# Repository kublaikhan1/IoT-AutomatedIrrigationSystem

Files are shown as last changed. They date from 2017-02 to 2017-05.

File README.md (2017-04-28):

## Concept Proposal

### High-level Concept:
Create an IoT indoor home irrigation system for potted plants using a Raspberry Pi and various hardware components. The system will feature two soil moisture sensors in two separate potted plants that will send real time analog data back to the Pi. Software on the Pi will monitor these sensor levels periodically; when levels fall below a certain threshold that constitutes “dry” soil, a signal will be sent to activate a peristaltic pump attached to the Pi. The pump will distribute water from a plastic reservoir to the plants that are “dry” (i.e. either one or both) until the moisture sensor input rises above the threshold, at which point the pump will deactivate. Sensor readings and water usage data will be viewable via a ThingSpeak interface as well as notifications from Twitter. Having two sensor/plant setups will hold as a proof of concept that multiple plants and sensors can be linked into this IoT system. 

## Operation and Interaction:
This project will stand out among other competitive irrigation systems by our ability to connect multiple separate potted plants. Other projects made watering systems for either one plant, or a single bed of many plants, so the challenge here is to maintain two or more individual plants. 

Using different plants requires the use of solenoid valves that can redirect the flow of water to the proper plant. The pump and the valves require 12VDC, which is more than the output of the RPi’s 5VDC, so a relay will be used to connect these devices with the Pi. When a valve needs to be opened and the pump turned on, the Pi will send 5VDC to the relay, which will enable the hardware on the other side of the relay. 

The soil moisture sensors record data in analog, which is not standard for the Pi, so an MCP3008 chip will be used, which takes up to eight separate analog inputs at a time, converting them to digital. Although we will only be proving the irrigation system works for two plants (i.e. two analog sensors), up to eight will be feasible using this chip.
One additional sensor will be placed in the water reservoir where the pump is located - a water level float switch. When the water level drops to a certain point, the sensor will trip, sending a signal to the Pi. We will link this with Twitter as well to send a notification to the user that the reservoir needs to be refilled.

## Required Hardware:
1. RPi - in this case, we’ll be using Elliot’s RPi2 and Hamad’s RPi3
2. 2x Analog Capacitive soil moisture sensors
3. 2x Solenoid valves 12VDC
4. 1x Peristaltic pump 12VDC
5. 1x MCP3008 chip for analog to digital conversion
6. 1x 5VDC 4-channel relay
7. 1x Water level sensor

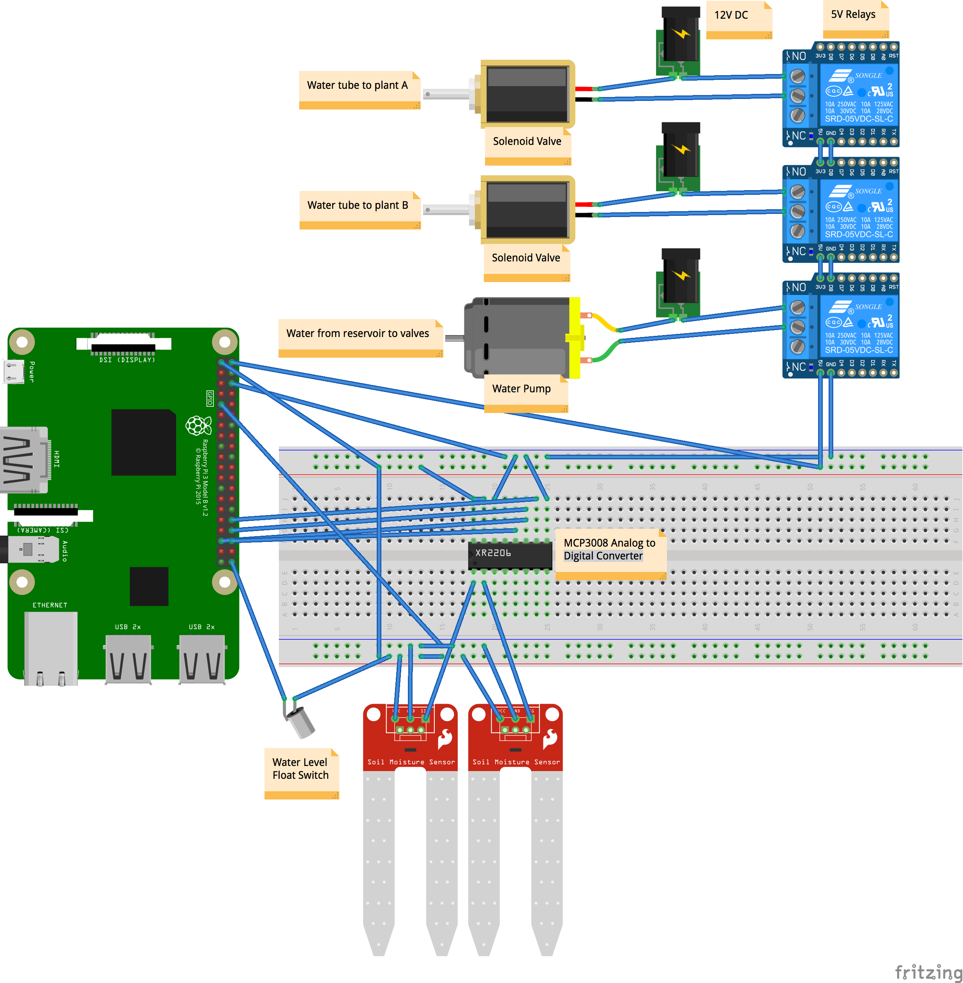
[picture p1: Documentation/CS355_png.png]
Optional Title


# Contributors
@hamadkh
@giese

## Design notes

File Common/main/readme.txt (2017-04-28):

/*
Module: Communication with ThingSpeak (on Linux) via TCP Socket
Author:  Pedro Bertoleti
Modified by: Hamad Khawaja, Elliot Giese
*/

INFORMATION FOR THINGSPEAK CHANNEL 
------------------------------------------

run:
----
make

./ThingSpeakC APIKEY [field1] [field2] ....... [fieldn]

CURRENT TEST APIKEY: 1J6Q9XGCJ3FJ456A

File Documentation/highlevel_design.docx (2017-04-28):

Elliot Giese

Hamad Khawja

CS 355 - Systems Programming

Part 2 - System Design

On it’s own, the Raspberry Pi can not read incoming analog data on GPIO pins. Since this irrigation system utilizes analog soil moisture sensors, an analog-to-digital converter is required. An MCP3008 chip is used to convert up to eight analog inputs into digital inputs for the Pi to read, and can either run on the Pi’s SPI hardware bus, or implemented on SPI via software. The diagram below depicts only two analog sensors connected to the chip, for the sake of space; however, up to eight can be used with this MCP3008 chip. Both the chip and the soil moisture sensors take 3.3V of power from the RPi 3V3 pin.

The soil sensors will periodically (~every 15 minutes) gather data values between 0 - 600 (with 0 constituting dry soil, and 600 wet) from each connected plant to send to the Pi. Based on programming logic enforced in a C-based program, the Pi will make a decision during these intervals to water the plant(s) or not. If the moisture value of a plant falls below a defined constant threshold (based on the type of plant input to the program on runtime), the Pi will turn on a water pump and particular solenoid valve associated with the dry plant.

Solenoid valves require 12VDC to activate, and are closed when power is off, and open when supplied power. The pump utilizes 120VAC, and is automatically on when plugged in (there is no on-off switch). By default, it’s flow rate is 80 gal/hr, but this can be adjusted manually with a dial on the side. Both solenoid valves and the pump will be connected to a 4-channel 5VDC relay, which in turn is connected to the Pi.

A 4-channel relay operates on 5VDC, which will be taken from the 5VDC pin on the Pi. Three GPIO pins, and GND will connect from the Pi to the relay. When the Pi sends a signal to turn on the pump over the GPIO line, 5VDC will activate the pump and valve relays. Relays allow low-power (5VDC) circuits to switch on higher-power (12VDC - 220VAC) circuits - in this case, the relay will activate the pump and one or both of the pump circuits. The pump will distribute water to one or both plants in short intervals until the next sensor reading returns a moisture value that has returned above the threshold. Flyback diodes may need to be included on the Pi side of the relay, as well as the pump and valve sides to prevent current from re-entering the devices in the wrong direction, damaging it.

Finally, a water float switch will be connected to the 3V3 pin of the Pi as well as a GPIO pin, which will monitor the water level of the basin that the pump is drawing water from. When the basin level falls below a certain value, the float switch will trip, sending a signal to the Pi. Upon receiving the signal, the Pi will send a Tweet to the user, informing them that the water levels are low, and should be refilled.

Collecting data from and interacting with GPIO pins in C will require including an open source library called wiringPi. Data interaction will be done via ThingSpeak, where the user can view daily summaries of water usage, power consumption, moisture levels, and watering times.

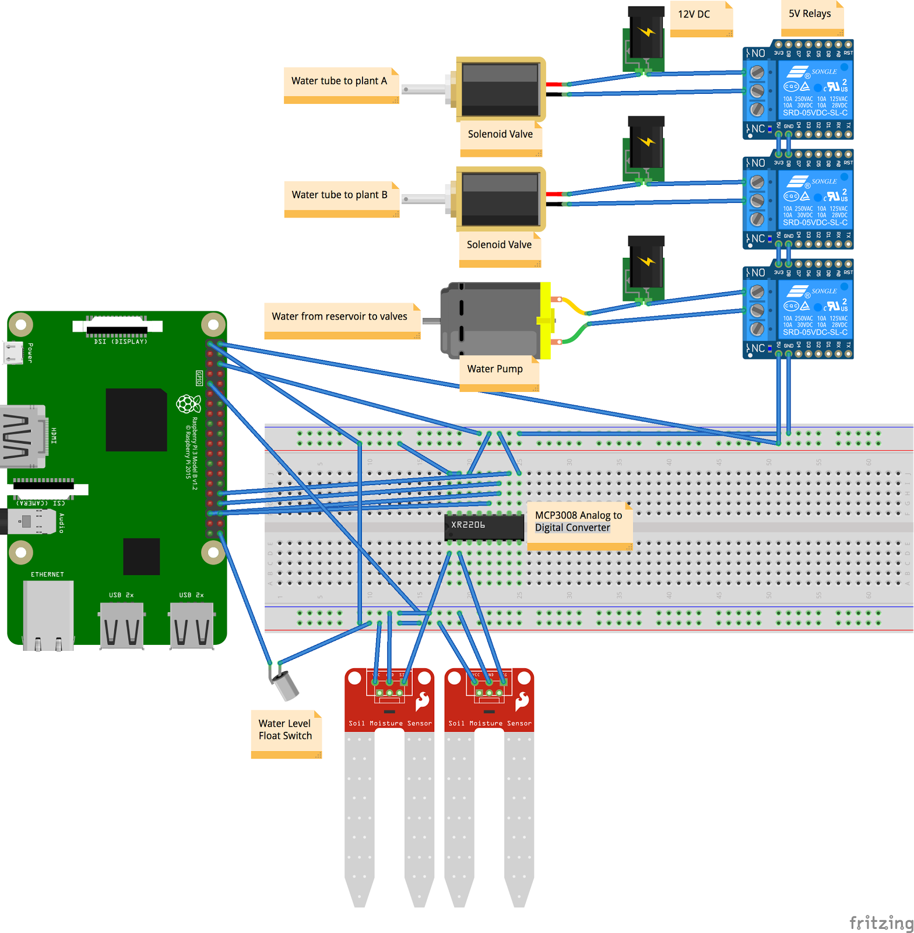
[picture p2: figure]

Wiring diagram of the circuit. Soil moisture sensors will be inserted into individual potted plants. Float switch will be in the reservoir of water. ½” clear vinyl tubing connects the pump to a T-joint, which in turn connects both of the solenoid valves. Valves use ½” male x ½” barbed connectors to attach vinyl tube, which then goes to plant. Each plant has one valve and one sensor associated.

BASIC FLOWCHART:

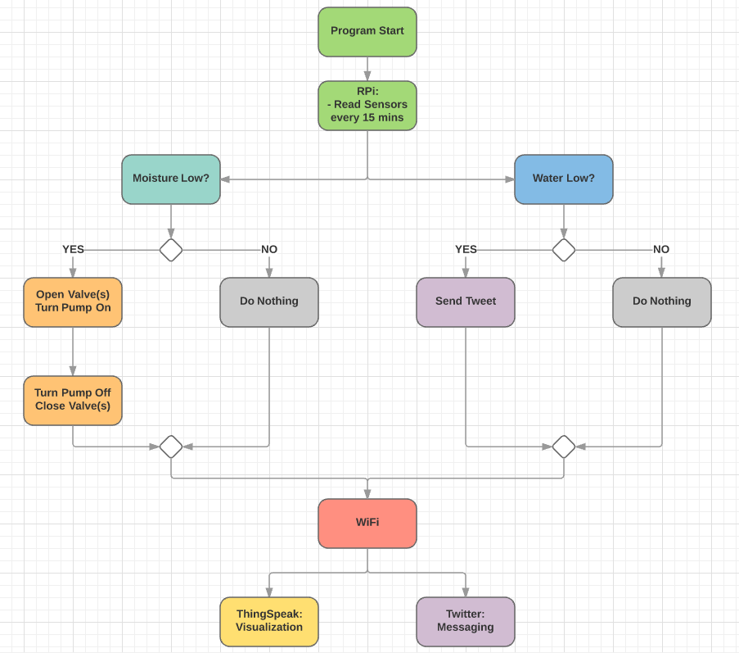
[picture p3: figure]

DATA FLOW:

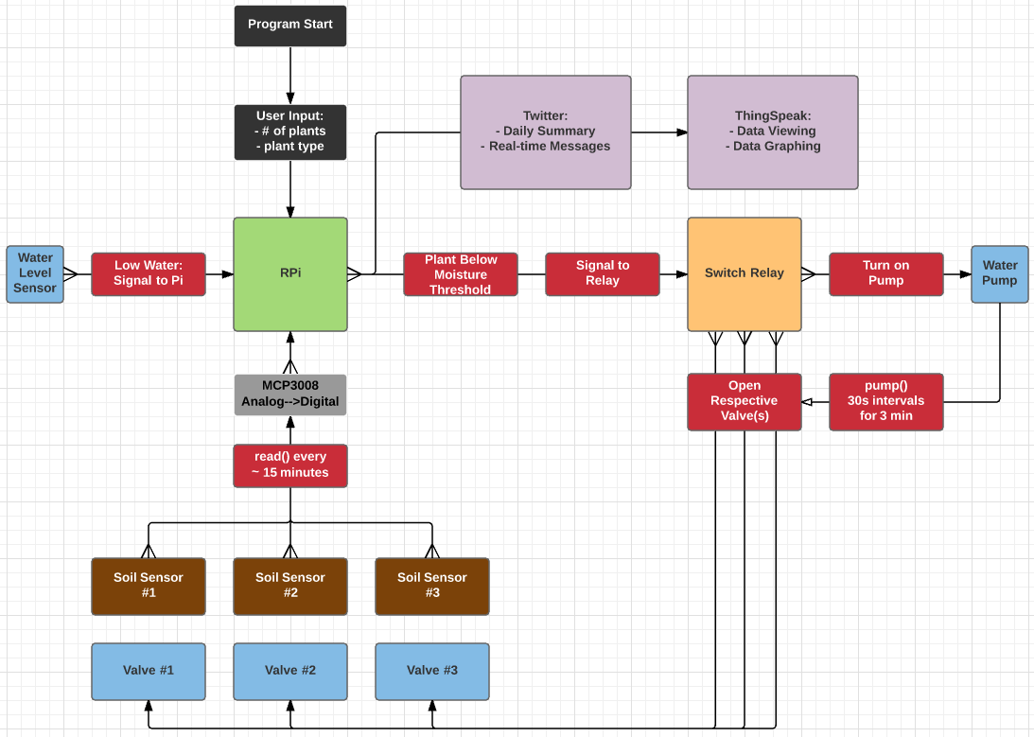
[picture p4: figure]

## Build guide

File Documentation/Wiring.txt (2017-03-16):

LCD Display
1  VSS  - Ground
2  VDD  - 5VDC
3  V0   - Ground
4  RS   - GPIO26, or PIN 24 on wiringPi, PIN 37 header
5  RW   - Ground
6  E    - GPIO21, or PIN XX on wiringPi, PIN 40 header
7  D0   - SKIP
8  D1   - SKIP
9  D2   - SKIP
10 D3   - SKIP
11 D4   - GPIO20, or PIN XX on wiringPi, PIN 38 header
12 D5   - GPIO16, or PIN XX on wiringPi, PIN 36 header
13 D6   - GPIO12, or PIN XX on wiringPi, PIN 32 header
14 D7   - GPIO25, or PIN XX on wiringPi, PIN 22 header
15 A    - 5VDC
16 K    - Ground

Float switch
When magnet is at bottom (low on water), circuit closes - i.e.
HIGH VOLTAGE
When magnet is floating at top (water level is good), circuit open - i.e.
LOW VOLTAGE
Pin 8 (4 on wiring)
Ground

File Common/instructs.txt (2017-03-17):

BY: HAMAD KHAWAJA

Installing GTK+ Library on RaspberryPi Linux
--------------------------------------------

sudo apt-get install libgtk2.0-dev
sudo apt-get install libgtk-3-dev

echo `pkg-config --cflags --libs gtk+-3.0`

Installing Glade
----------------

sudo apt-get install glade (GUI EDITOR)

Installing Geany
----------------

sudo apt-get isntall geany (TEXT EDITOR/ NOT MANDATORY)

Dependencies
------------
gcc -o main gui.c `pkg-config --cflags --libs gtk+-3.0`

running using make 
------------------

make 
make clean

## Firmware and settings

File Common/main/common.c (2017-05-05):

#include <time.h>
#include <stdio.h>
#include <stdlib.h>
#include <stdint.h>
#include <unistd.h>
#include <mcp3004.h>
#include <pthread.h>
#include <wiringPi.h>
#include "ThingSpeakLinux.h"


/* Definitions for MCP3004/8 chipset */
#define BASE 100
#define SPI_CH 0

/* Definitions for 4-chan relay GPIO pins */
#define RELAY1 21
#define RELAY2 22
#define RELAY3 23
#define RELAY4 24

/* Float Switch GPIO pin */
#define FL_SWI 4

/* Define number of plants */
#define NUM_PLANTS 2

/* Definitions for DHT22 temp/hum sensor */
#define MAX_TIMINGS 85
#define DHT_PIN 5

void start();
int getWaterLevel();
void *soilThread();
void getSoilMoisture(int[],float[]);
double getWaterUsage(double);
void read_dht_data();
void temperatureReadings();
void activateRelays();

int data[5] = { 0, 0, 0, 0, 0 };
int soilVals[NUM_PLANTS] = {1000};
float soilPercent[NUM_PLANTS] = {100.0};
float humtemp[3] = {0.0};
float FieldsArrayPlant1[6]={0.0};
float FieldsArrayPlant2[6]={0.0};
int waterLvl;



int main(void)
{
	pthread_t pt;

	if(wiringPiSetup() == -1)
	{
		printf("wiringPi setup failed");
		return 1;
	}
	
	start();
	pthread_create(&pt, NULL, soilThread, NULL);
	
	int count = 1;
	
	while(count == 1)
	{		
		if(!waterLvl)
		{
			
			//printf("Exiting program!\n");
			//count++;
			//exit(1);
		}
		
		//activateRelays();
		sleep(5);
	}

	return 0;
}


/* ------------------------------------------------
 * Initialize Analog-to-Digital Converter
 * Initialize GPIO pin modes for each relay
 * Initialize GPIO pin for float switch
 * -----------------------------------------------*/
 
void start()
{
	digitalWrite(FL_SWI, HIGH);
	mcp3004Setup(BASE, SPI_CH);
	pinMode(RELAY1, OUTPUT);
	pinMode(RELAY2, OUTPUT);
	pinMode(RELAY3, OUTPUT);
	pinMode(RELAY4, OUTPUT);
	pinMode(FL_SWI, OUTPUT);
}


/* ------------------------------------------------
 * Returns 0 if water level is low, 1 otherwise
 * -----------------------------------------------*/
 
int getWaterLevel()
{
	return digitalRead(FL_SWI);
}


/* ---------------------------------------------------------------
 * Reads channels 0-7 on MCP3008 chip over Serial 
 * Peripheral Interface (SPI).
 * Each analogue sensor returns a value from 0 ~ 600
 * Value of    0 is dry (i.e. air)
 * Value of ~600 is wet (i.e. pure water)
 * --------------------------------------------------------------*/
 
void getSoilMoisture(int soilVals[], float soilPercent[])
{
	int chan, i;
	int sum = 0;
	
	for(chan = 0; chan < NUM_PLANTS; ++chan)
	{
		
		for(i = 0; i < 2000; i++)
			sum += (1023 - analogRead(BASE + chan));
			
		soilVals[chan] = sum / 2000;
		soilPercent[chan] = (float) ((soilVals[chan] / 800.0) * 100.0);

		if(soilVals[chan] < 800)
			printf("PLANT #%d moisture: %3.2lf%\n", chan+1, soilPercent[chan]);
		
		sum = 0;	
	}
}


/* ------------------------------------------------
 * Returns the amount of water  
 * used by the pump in Liters
 * Pump waters at a rate of 300L/H
 * timeWatered is recorded in seconds
 * -----------------------------------------------*/
 
double getWaterUsage(double timeWatered)
{
	return 300 * timeWatered / 3600;
}


/* ------------------------------------------------
 * Thread function which will collect the soil data  
 * and temperature data
 * If the water level is LOW, then the thread will
 * die
 * -----------------------------------------------*/
 
void *soilThread()
{
	char apiKey1[] = "KQ0EYMR9E7QY7500";
	char apiKey2[] = "Z8725FTQG09C3FIK";
	
	while(1)
	{
		printf("Water Level = %d\n\n", waterLvl = getWaterLevel());
		if(!waterLvl)
		{
			printf("---  Water level is low  ---\n");
			printf("--- Pump will not activate ---\n\n");
		}
		getSoilMoisture(soilVals, soilPercent);
		temperatureReadings();
		
		activateRelays();
		
		int i;
		for(i = 0; i < 6; i++)
		{
			SendDataToThingSpeak(6, &FieldsArrayPlant1[i],apiKey1,sizeof(apiKey1));
			SendDataToThingSpeak(6, &FieldsArrayPlant2[i],apiKey2,sizeof(apiKey2));
		}
		
		printf("\n-------------------------------------------\n\n");
		
		sleep(3);
	}

	return NULL;
}


/* -----------------------------------------------------
 * Function to take 250 temperature / humidity  
 * readings based on the read_dht_data() function
 * The sensor's data is sometimes corrupt, which is the
 * result of a faulty sensor - even the read_dht_data()
 * function accounts for this... So 250 measurements
 * will ensure that at least one value is recorded
 * ----------------------------------------------------*/
 
void temperatureReadings()
{
	int count = 0;
	while(1)
	{
		read_dht_data();
		if( !( humtemp[0] == 0.0 || humtemp[1] == 0.0 || humtemp[2] == 0.0 ) || (humtemp[0] >= 100.0 || humtemp[1] >= 100.0) || count > 249)
		{
			break;
		}
		count++;
	}
}


/* ----------------------------------------------------
 * Function to turn on the relays, which are connected
 * to the solenoid vales and the water pump.
 * If the soil moisture percentage is lower than 50%
 * for a given plant, the relay/valve associated with
 * that plant will open, and the pump will turn on.
 *
 * Function also records amount of water used, and
 * length of time that plants were watered.
 * ---------------------------------------------------*/
 
void activateRelays()
{
	double timeWatered = 0.0; double amtWatered = 0.0;
	int relays[] = {RELAY1,RELAY2,RELAY3,RELAY4};
	int numPlantsWatered=0; int numRelays=4;
	time_t waterTimeStart, waterTimeEnd;
	int i;
	
	for(i = 0; i < NUM_PLANTS; i++)
	{
		if(soilPercent[i] < 50.0 && waterLvl)
		{
			time(&waterTimeStart);
			digitalWrite(relays[i], LOW);
			digitalWrite(relays[2], LOW);
			printf("PLANT valve #%d open\n", (i+1) );
			//printf("PUMP ON \n" );
			
			delay(5000);
			
			digitalWrite(relays[i], HIGH);
			digitalWrite(relays[2], HIGH);
			printf("PLANT valve #%d closed\n\n", (i+1) );
			//printf("PUMP OFF \n");
			
			time(&waterTimeEnd);
			timeWatered = difftime(waterTimeEnd, waterTimeStart);
			amtWatered += getWaterUsage(timeWatered);
			numPlantsWatered++;
		}
	}
	
	// Fill ThingSpeak Arrays
	FieldsArrayPlant1[0] = soilPercent[0];
	FieldsArrayPlant1[1] = humtemp[2];
	FieldsArrayPlant1[2] = humtemp[0];
	FieldsArrayPlant1[3] = timeWatered;
	FieldsArrayPlant1[4] = amtWatered;
	FieldsArrayPlant1[5] = waterLvl;
	
	FieldsArrayPlant2[0] = soilPercent[1];
	FieldsArrayPlant2[1] = humtemp[2];
	FieldsArrayPlant2[2] = humtemp[0];
	FieldsArrayPlant2[3] = timeWatered;
	FieldsArrayPlant2[4] = amtWatered;
	FieldsArrayPlant2[5] = waterLvl;
	
	if(waterLvl)
	{
		printf("Time watered: %.2lf seconds\n", timeWatered*numPlantsWatered);
		printf("Amount of water used: %.2lf Liters\n\n\n", amtWatered);
	}
	else
	{
		printf("Time watered: %.2lf seconds\n", timeWatered*numPlantsWatered);
		printf("Amount of water used: %.2lf Liters\n\n\n", amtWatered);
	}
}


/*--------------------------------------------------------------------------------------
 *			:::IMPORTANT NOTE:::
 * 
 * This code was taken from the following source in order to avoid
 * re-inventing the wheel. The sensor used is DIGITAL, which is why
 * the code to extract meaningful data is so long. Using an ANALOG
 * sensor would have avoided the need to borrow this source code
 *
 * www.uugear.com/portfolio/read-dht1122-temperature-humidity-sensor-from-raspberry-pi/
 *
 *-------------------------------------------------------------------------------------*/
 
void read_dht_data()
{
	uint8_t laststate	= HIGH;
	uint8_t counter		= 0;
	uint8_t j		= 0, i;
	float hum, cel, far;

	data[0] = data[1] = data[2] = data[3] = data[4] = 0;

	/* pull pin down for 18 milliseconds */
	pinMode( DHT_PIN, OUTPUT );
	digitalWrite( DHT_PIN, LOW );
	delay( 18 );

	/* prepare to read the pin */
	pinMode( DHT_PIN, INPUT );

	/* detect change and read data */
	for ( i = 0; i < MAX_TIMINGS; i++ )
	{
		counter = 0;
		while ( digitalRead( DHT_PIN ) == laststate )
		{
			counter++;
			delayMicroseconds( 1 );
			if ( counter == 255 )
			{
				break;
			}
		}
		laststate = digitalRead( DHT_PIN );

		if ( counter == 255 )
			break;

		/* ignore first 3 transitions */
		if ( (i >= 4) && (i % 2 == 0) )
		{
			/* shove each bit into the storage bytes */
			data[j / 8] <<= 1;
			if ( counter > 16 )
				data[j / 8] |= 1;
			j++;
		}
	}

	/*
	 * check we read 40 bits (8bit x 5 ) + verify checksum in the last byte
	 * print it out if data is good
	 */
	if ( (j >= 40) &&
	     (data[4] == ( (data[0] + data[1] + data[2] + data[3]) & 0xFF) ) )
	{
		float h = (float)((data[0] << 8) + data[1]) / 10;
		if ( h > 100 )
		{
			h = data[0];	// for DHT11
		}
		float c = (float)(((data[2] & 0x7F) << 8) + data[3]) / 10;
		if ( c > 125 )
		{
			c = data[2];	// for DHT11
		}
		if ( data[2] & 0x80 )
		{
			c = -c;
		}
		float f = c * 1.8f + 32;
		printf( "\n\nHumidity = %.1f %% Temperature = %.1f *C (%.1f *F)\n\n", h, c, f );
		
		hum = h;
		cel = c;
		far = f;
	}
	humtemp[0] = hum;
	humtemp[1] = cel;
	humtemp[2] = far;
}

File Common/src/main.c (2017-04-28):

#include <gtk/gtk.h>
#include <stdlib.h>

GtkWidget *g_lbl_hello;
GtkWidget *btn_START;
GtkWidget *btn_STOP;

int running = 0;

int main(int argc, char *argv[])
{
    GtkBuilder      *builder; 
    GtkWidget       *window;


    gtk_init(&argc, &argv);

    builder = gtk_builder_new();
    
 
    
    gtk_builder_add_from_file (builder, "glade/window_main.glade", NULL);

    window = GTK_WIDGET(gtk_builder_get_object(builder, "window_main"));
    gtk_builder_connect_signals(builder, NULL);
    
    g_lbl_hello = GTK_WIDGET(gtk_builder_get_object(builder, "lbl_hello"));

    g_object_unref(builder);

    gtk_widget_show(window);                
    gtk_main();

    return 0;
}

void on_btn_START_clicked()
{	
	if(running == 0)
	{
		gtk_label_set_text(GTK_LABEL(g_lbl_hello), "ON");
		system("lxterminal -e main/watering");
		running = 1;
	}
}

void on_btn_STOP_clicked()
{
	if(running == 1)
	{
    		gtk_label_set_text(GTK_LABEL(g_lbl_hello), "OFF");
    		system("./stop.sh");
    		running = 0;
	}
}

// called when window is closed
void on_window_main_destroy()
{
    system("./stop.sh");
    gtk_main_quit();
}

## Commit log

2017-03-16 Wiring.txt
    Wiring descriptions
2017-03-30 Added temperature file
2017-03-30 Threading implementation concept
2017-04-07 Added threading
2017-04-28 final straw
    [CS355.fzz]
2017-04-28 Revert "Web dev"
    [CS355.fzz]
